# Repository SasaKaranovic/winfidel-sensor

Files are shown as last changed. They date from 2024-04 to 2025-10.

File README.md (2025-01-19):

# WInFiDEL Sensor

**W**ireless
**In**line
**Fi**lament
**D**iameter
**E**stimator
**L**ow-cost
Sensor

## What is WInFiDEL?

WInFiDEL (https://www.youtube.com/watch?v=FzXX6JxIw_Q "WInFiDEL - DIY 3D Printing Filament Diameter Sensor")

[WInFiDEL Video](https://www.youtube.com/watch?v=FzXX6JxIw_Q)

WInFiDEL is an DIY open-source open-hardware Wireless 3D printing filament diameter sensor.

This design is heavily inspired by the design previously published by Made with Layers (Thomas Sanladerer) (video: https://www.youtube.com/watch?v=RYgdLPe_T0c)

## Can I build my own WInFiDEL sensor?

Yes! All the source files (hardware and firmware) are available in this repository.

## Can I purchase WInFiDEL PCBA?

Yes! It's available on the [web shop](https://shop.sasakaranovic.com/products/winfidel).

## Where can I find documentation?

WInFiDEL documentation can be found on the [official documentation page](https://docs.sasakaranovic.com/winfidel/).

## Screenshots

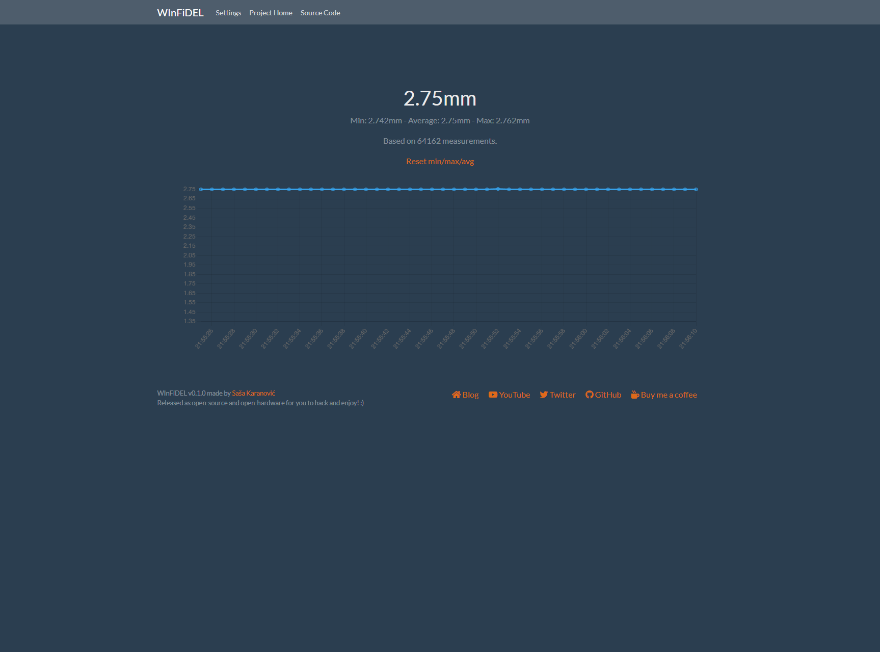
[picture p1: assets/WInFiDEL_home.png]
Home


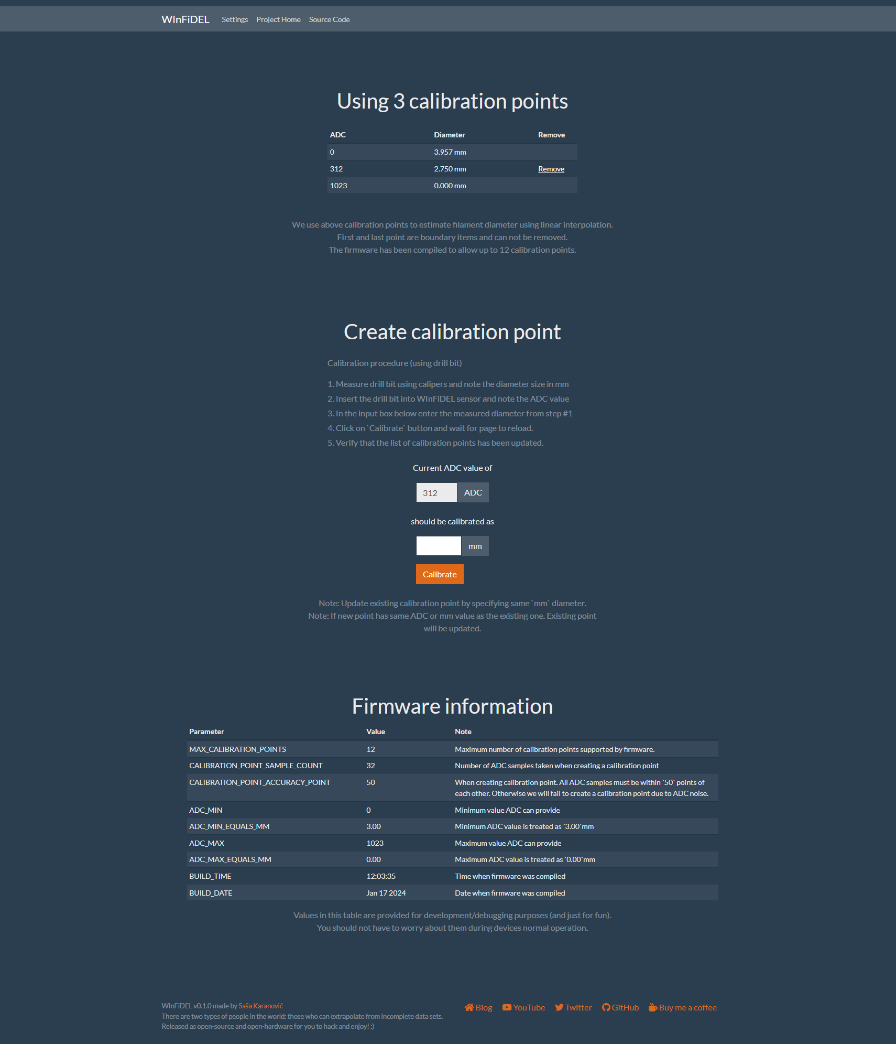
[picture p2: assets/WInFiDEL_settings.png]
Calibration


## Sasa Karanovic

<a href="https://sasakaranovic.com/" target="_blank" title="Sasa Karanovic Home Page"> Home Page</a> &nbsp;&middot;&nbsp;
<a href="https://youtube.com/c/sasakaranovic" target="_blank" title="Sasa Karanovic on YouTube"> YouTube</a> &nbsp;&middot;&nbsp;
<a href="https://github.com/sasakaranovic" target="_blank" title="Sasa Karanovic on GitHub"> GitHub</a> &nbsp;&middot;&nbsp;
<a href="https://twitter.com/_sasakaranovic_" target="_blank" title="Sasa Karanovic on Twitter"> Twitter</a> &nbsp;&middot;&nbsp;
<a href="https://instagram.com/_sasakaranovic_" target="_blank" title="Sasa Karanovic on Instagram"> Instagram</a> &nbsp;&middot;&nbsp;
<a href="https://github.com/sponsors/SasaKaranovic" target="_blank" title="Sponsor on GitHub"> Sponsor on GitHub</a>

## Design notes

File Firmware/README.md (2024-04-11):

# How to build firmware

For our firmware development, we are going to use Arduino. Mainly because it's user friendly, easy to use and
most hobbyists are familiar with it or have already used it. While we could build the same or even more efficient
firmware using bare-metal C and ESP-IDF, we are going to stick with Arduino and hope that this allows the project to be
more friendly and easier to use/modify by wider DIY/hacker community.

## How can I build/compile firmware?

### 1. Install PlatformIO
Installing PlatformIO CLI is pretty straight-forward and also well documented for Windows, Linux and MacOS.
You will need to follow few steps and get PlatformIO CLI installed, detailed tutorial can be found at https://platformio.org/install/cli
Make sure to install [PlatformIO Core](https://docs.platformio.org/en/latest//core/installation.html#installation-methods 'https://docs.platformio.org/en/latest//core/installation.html#installation-methods') and allso that it is available trough [shell](https://docs.platformio.org/en/latest//core/installation.html#piocore-install-shell-commands 'PlatformIO Core - Install Shell Commands¶').

### 2. Build firmware
Open shell/command-prompt and navigate to 'Firmware/platformio' folder.

1. Compile and upload the firmware with `pio run --target upload --upload-port <COM-PORT>`. Make sure to replace `<COM-PORT>` with your ESP32's COM port (ie COM1 or /dev/ttyACM0)
2. Upload the file system (Web page) with `pio run --target uploadfs --upload-port <COM-PORT>`, again replace `<COM-PORT>` with your ESP32's COM port.
3. Restart/power-cycle your board

Every time you make a firmware change, you need to run step #1.
Every time you make a change to the web page (anything inside `data` folder) you only need to run step #2.

[<- Go back to repository root](../README.md)

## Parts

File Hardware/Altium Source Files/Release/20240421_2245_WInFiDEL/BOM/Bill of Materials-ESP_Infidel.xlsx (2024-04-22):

Designator | Value | Description | Distributor | Distributor Part Number | Manufacturer | Manufacturer Part Number | Quantity | Footprint
A1 |  | RF ANT 2.45GHZ CHIP SOLDER SMD | LCSC | ANT3216LL00R2400A | YAGEO | ANT3216LL00R2400A | 1 | ANT3216LL00R2400A
C1, C6 | 22uF | Capacitor | LCSC | C602037 | Samsung Electro-Mechanics | CL21A226MAYNNNE | 2 | 0805
C2, C5, C15, C24, C25 | 10uF | Capacitor | LCSC | C15850 | Samsung Electro-Mechanics | CL21A106KAYNNNE | 5 | 0603 - CAP
C3, C4, C11, C13, C16, C20, C21, C22, C23 | 100n | Capacitor | LCSC | C1591 | Samsung Electro-Mechanics | CL10B104KB8NNNC | 9 | 0603 - CAP
C9, C10, C12, C14, C17 | 1u | Capacitor | LCSC | C559769 | YAGEO | CC0603KRX7R9BB105 | 5 | 0603 - CAP
C18, C19 | 8pF | Capacitor | LCSC | C327316 | YAGEO | CC0603CRNPO9BN8R0 | 2 | 0603 - CAP
P1 |  | 3A 1 Surface Mount 16P Female -25℃~+85℃ Type-C SMD USB Connectors ROHS | LCSC | C2927039 | DEALON | USB-TYPE-C-019 | 1 | GCT_USB4105-GF-A
R1, R2, R5, R6, R7, R8 | 5.1K | Resistor | LCSC | C105580 | YAGEO | RC0603FR-075K1L | 6 | 0603
R3, R4 | 27R | Resistor | LCSC | C137753 | YAGEO | RC0603FR-0727RL | 2 | 0603
R9, R10, R12 | 2K2 | Resistor | LCSC | C125931 | YAGEO | AC0603FR-072K2L | 3 | 0603
R11 | 0R | Resistor | LCSC | C95177 | YAGEO | RC0603JR-070RL | 1 | 0603
SW1, SW2 |  | 50mA Surface Mount SPST 100MΩ 100,000 Times 12V 160gf@±50gf SMD Tactile Switches ROHS | LCSC | C7498203 | Lian Xin Technology | XDTD-0304-215 | 2 | Switch-XDTD-0304-215
U1 |  | 600mA null 3.3V positive 6V SOT-25 Linear Voltage Regulators (LDO) ROHS | LCSC | C526385 | Diodes Incorporated | AP7366-33W5-7 | 1 | SOT-23-5
U2 |  | Ultra-Low-Power SoC with RISC-V Single-Core CPU 2.4 GHz Wi-Fi (802.11 b/g/n) and Bluetooth® 5 (LE) | LCSC | C2858491 | Espressif Systems | ESP32-C3FH4 | 1 | QFN50P500X500X100_HS-33N
U3 |  | Hall Effect Sensor Single Axis Radial Lead | LCSC | C266124 | Texas Instruments | DRV5055A3QLPGM | 1 | SS490A
U4 |  | 10 Bit Analog to Digital Converter 1 Input 1 SAR SOT-23-5 | LCSC | C625475 | Microchip Technology | MCP3221A5T-E/OT | 1 | SOT95P270X145-5N
X1 |  | 40MHz 9pF ±10ppm SMD2016-4P Crystals ROHS | LCSC | C2929402 | TROQ | R940000171 | 1 | XTAL-4LEAD-2016

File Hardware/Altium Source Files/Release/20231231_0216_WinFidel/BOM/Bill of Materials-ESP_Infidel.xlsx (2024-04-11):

Designator | Description | Distributor | Distributor Part Number | Manufacturer | Manufacturer Part Number | Quantity
A1 | RF ANT 2.45GHZ CHIP SOLDER SMD | LCSC | ANT3216LL00R2400A | YAGEO | ANT3216LL00R2400A | 1
C1, C6 | Capacitor | DigiKey | 1276-CL21A226MAYNNNECT-ND | Samsung Electro-Mechanics | CL21A226MAYNNNE | 2
C2, C5 | Capacitor | DigiKey | 1276-2891-1-ND | Samsung Electro-Mechanics | CL21A106KAYNNNE | 2
C3, C4 | Capacitor | DigiKey | 1276-1009-1-ND | Samsung Electro-Mechanics | CL10B103KB8NNNC | 2
C7, C8, C9, C10, C11, C12, C13, C14, C15, C16, C17, C18, C19, C20, C21, C22, P2, R1, R2, R3, R4, R6, R7, R8, R9, R10, R11, R12, U2 | Capacitor, Header, 5-Pin, Resistor, Ultra-Low-Power SoC with RISC-V Single-Core CPU 2.4 GHz Wi-Fi (802.11 b/g/n) and Bluetooth® 5 (LE) | [NoValue], DigiKey, LCSC | [NoValue], C2858491 | [NoValue], Espressif Systems |  | 29
P1 | 3A 1 Surface Mount 16P Female -25℃~+85℃ Type-C SMD USB Connectors ROHS | LCSC | C2927039 | DEALON | USB-TYPE-C-019 | 1
SW1, SW2 | 50mA Surface Mount SPST 100MΩ 100,000 Times 12V 160gf@±50gf SMD Tactile Switches ROHS | LCSC | C7498203 | Lian Xin Technology | XDTD-0304-215 | 2
U1 | 600mA null 3.3V positive 6V SOT-25 Linear Voltage Regulators (LDO) ROHS | LCSC | C526385 | Diodes Incorporated | AP7366-33W5-7 | 1
U3 | Hall Effect Sensor Single Axis Radial Lead | DigiKey | 296-DRV5055A2QLPGMCT-ND | Texas Instruments | DRV5055A2QLPGM | 1
U4 | 10 Bit Analog to Digital Converter 1 Input 1 SAR SOT-23-5 | DigiKey | MCP3021A5T-E/OTCT-ND | Microchip Technology | MCP3021A5T-E/OT | 1
X1 | 40MHz 9pF ±10ppm SMD2016-4P Crystals ROHS | LCSC | C2929402 | TROQ | R940000171 | 1

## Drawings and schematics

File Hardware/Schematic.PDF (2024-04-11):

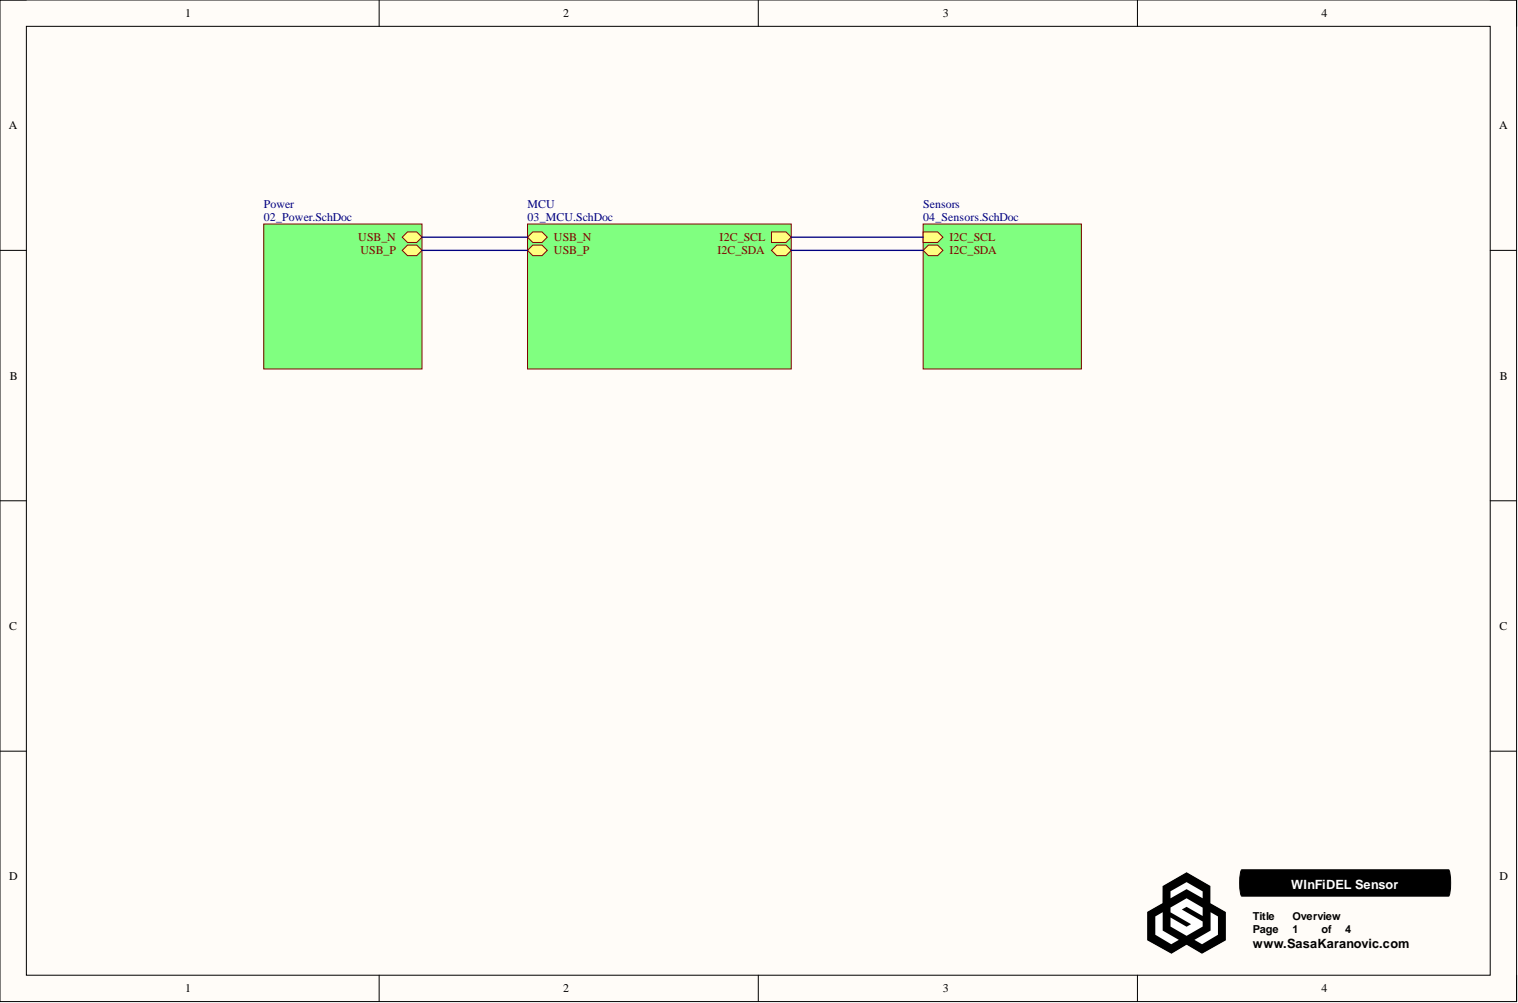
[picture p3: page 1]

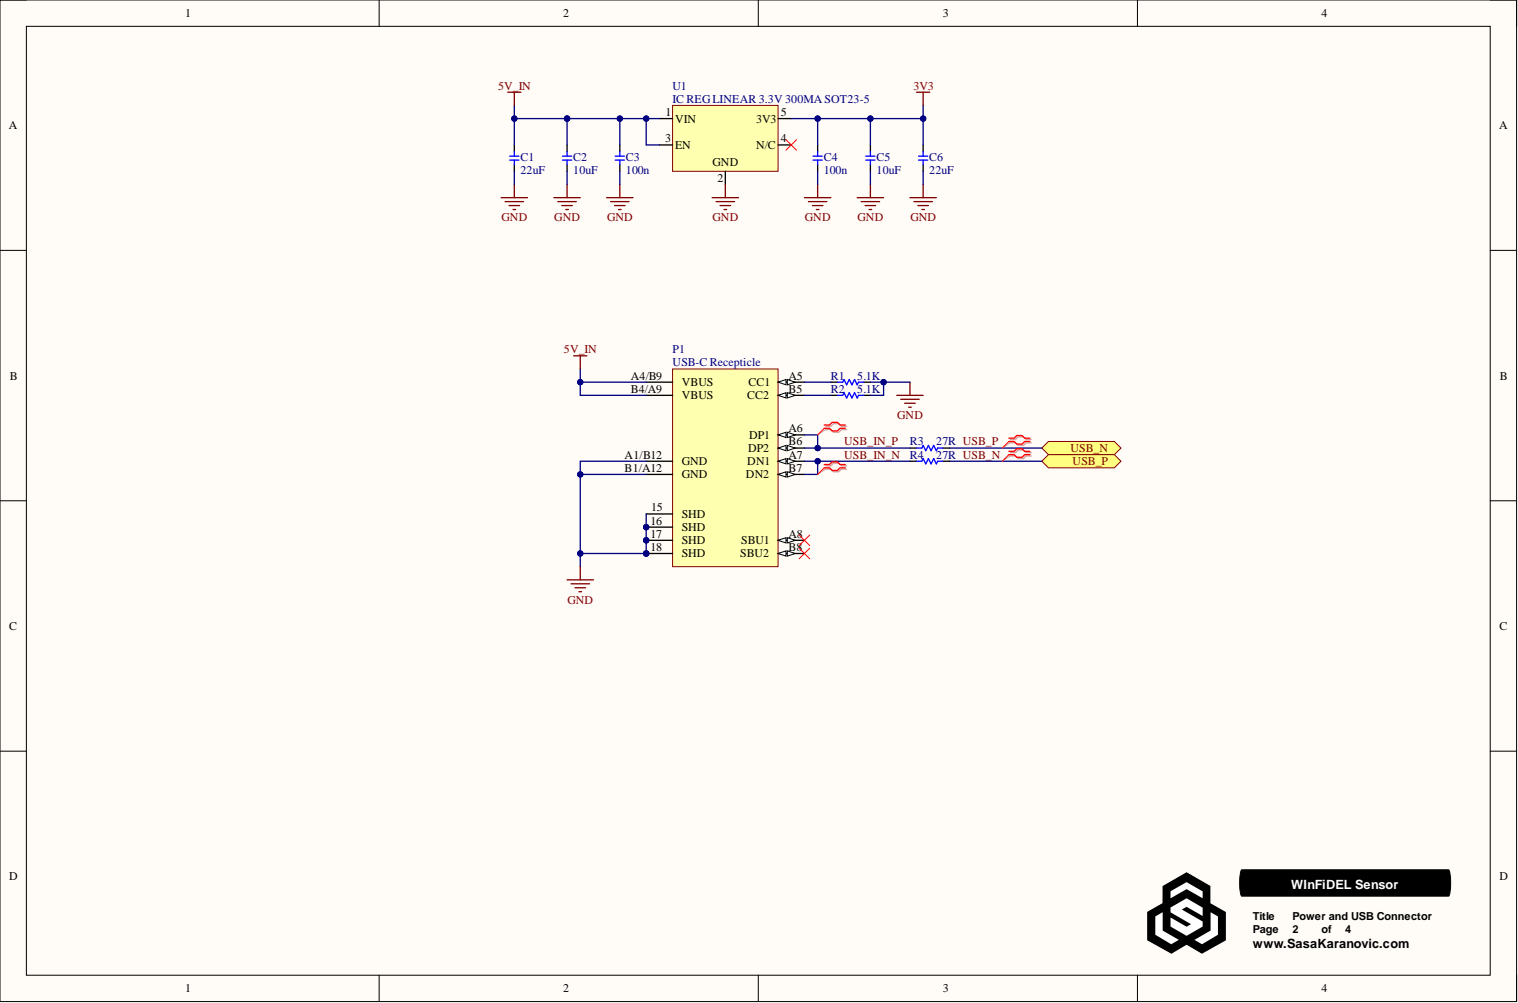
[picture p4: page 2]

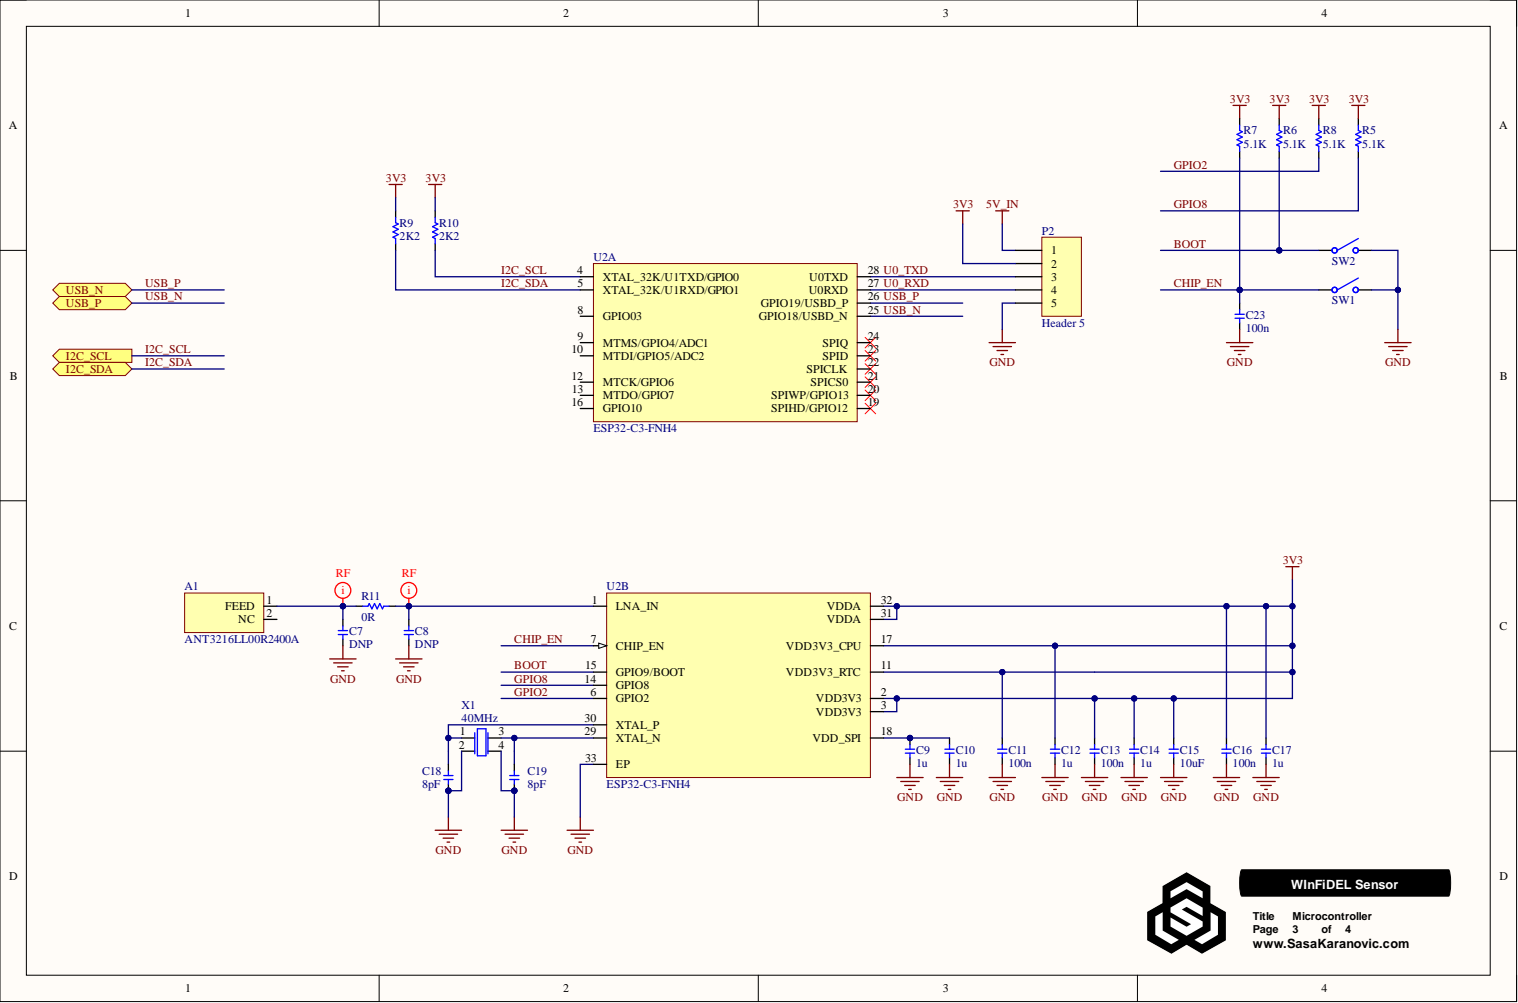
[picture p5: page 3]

GPIO2

GPIO8

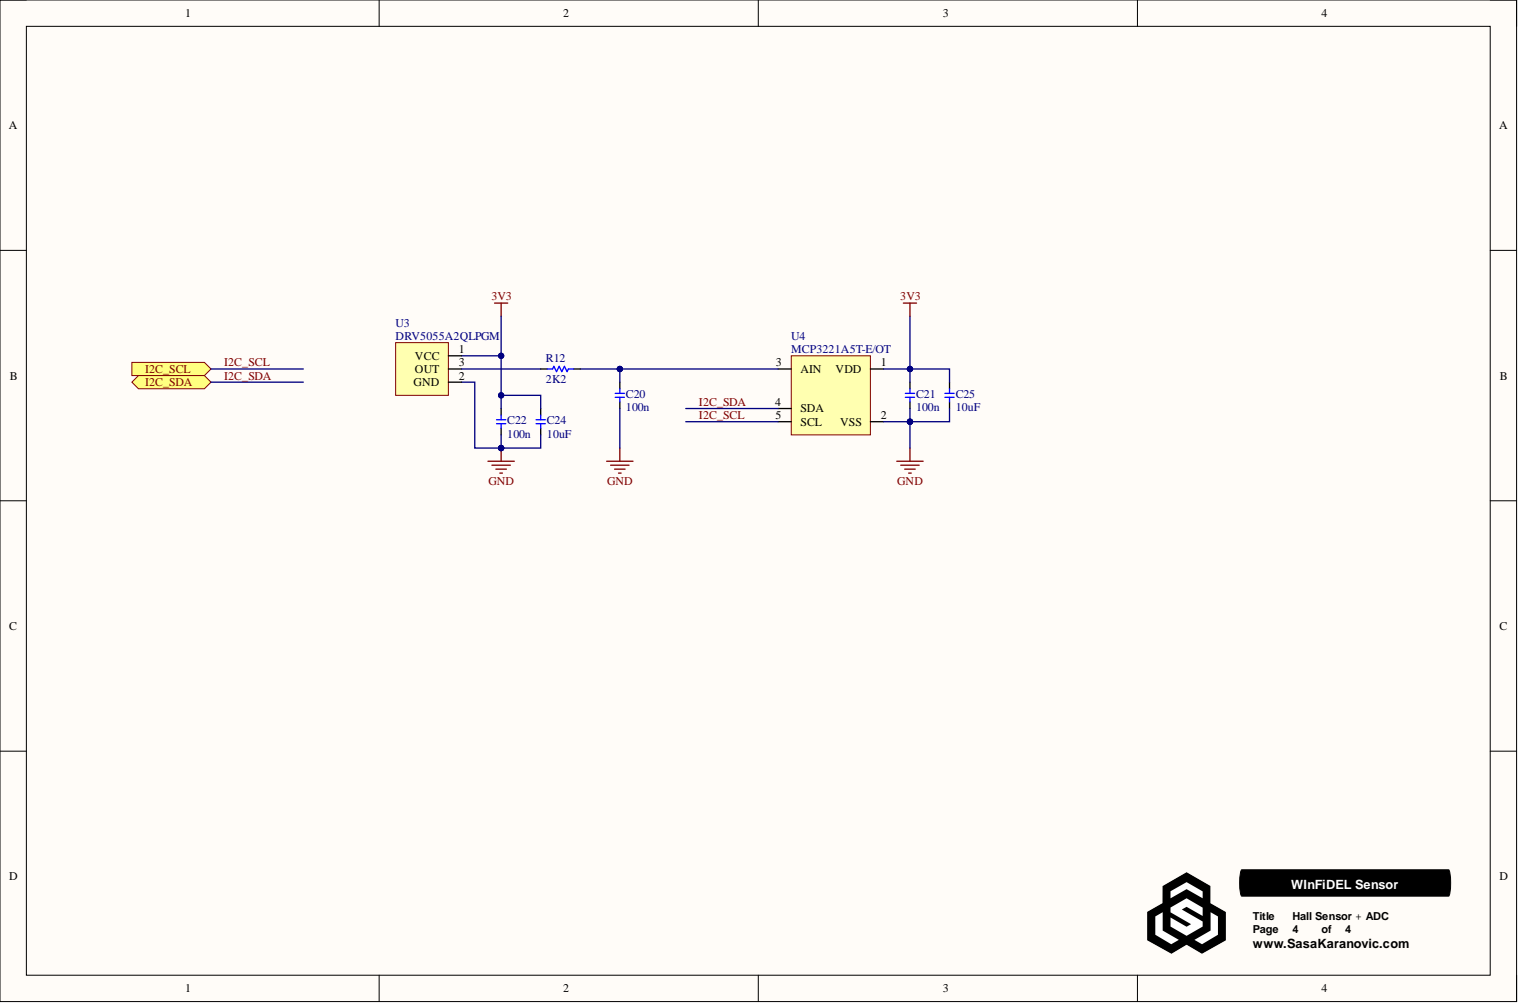
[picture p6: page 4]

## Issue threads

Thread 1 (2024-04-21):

Provided Gerber does not match Altium Data

cad435, 2024-04-21:
through sheer coincidence I just found out:

Just an example:

Gerber Data
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

Altium Data:
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

SasaKaranovic, 2024-04-22:
Thanks for mentioning this! I have just exported another gerber release that contains latest design. So everything should be good to go now.

If you look at the Gerbers, the silkscreen says "2023-DEC" but the Altium files have "2024-FEB".
This release was "rushed" in order to make sure people have all the source files available before Stefan's video goes live.

Closed 2024-04-22.

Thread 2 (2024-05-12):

LittleFS mount fail on new device

cad435, 2024-05-12:
Hello!

After building the devices (PnP as per BOM, used JLCPCBA) i get the following error:

```Starting...
*wm:AutoConnect
*wm:Connecting to SAVED AP: ***
*wm:connectTimeout not set, ESP waitForConnectResult...
*wm:AutoConnect: SUCCESS
*wm:STA IP Address: 192.168.178.72
Connected.
Starting LittleFS...E (11254) esp_littlefs: ./components/esp_littlefs/src/littlefs/lfs.c:1367:error: Corrupted dir pair at {0x0, 0x1}

E (11255) esp_littlefs: mount failed,  (-84)
E (11258) esp_littlefs: Failed to initialize LittleFS
[ 11148][E][LittleFS.cpp:98] begin(): Mounting LittleFS failed! Error: -1
An Error has occurred while mounting LittleFS
```

Any thoughts what went wrong?

cad435, 2024-05-12:
Just realized I forgot to build and upload the filesystem contents...

PEBCAK error I suppose :)

SasaKaranovic, 2024-05-12:
Been there done that. :)
Glad you figured it out. Let me know how it works.

Would you mind sharing how much did the PCBA run cost?
I know there are others that are interested in ordering these. I received couple of emails asking how much would it cost to make 1/5/10 of these through one of the online PCB services.

cad435, 2024-05-12:
Sure!

5 pcs cost me 36.84€ shipped.

Mind you, the USB-C connector, ADC, LDO, the tactile swithces and the 8pf capacitors I soldered myself. I have those laying around and did not want to spend the additional cost on those.
The problem is, those are "non standard" components for JLC so they take 3$ setup fee per component, which would increase the cost by 15$.
I was willing to take that for the ESP as I had not laying those around.

if you go all in I'd suppose you'll end up on about 50-60€ shipped for 5 pcs and about 90-100€ for 10pcs.

SasaKaranovic, 2024-05-12:
Awesome! Thank you for sharing this. I'm sure others will be happy to have a rough estimate on how much everything cost.

Closed 2024-05-12.

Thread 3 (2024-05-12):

Hall Sensor Reversed

cad435, 2024-05-12:
It should be noted somewhere, that the hall sensor should be mounted the other way round, compared to the original INFIDEL Sensor.

Top-PCB is the original, bottom PCB is WinFIDEL

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

Therefore the Hall-effect sensor must be glued in "upside down" compared to the original.

 - cad435

SasaKaranovic, 2024-05-13:
Hey @cad435

Please note that while WInFiDEL is inspired by InFiDEL, it is not identical, obviously.
If you flip the WInFiDEL board, you should see the 3V3, GND and OUT markings for that IC.

There are two ways you can figure out which components is on which side.
- Manually: If you use silkscreen as your guide, there is silkscreen on top AND bottom side. On the bottom side there is silkscreen that indicates the sensor pinout and also U3 that indicates that hall effect sensor is on the bottom.
- Production: Pick and Place file indicates that the U3 is on the bottom side.

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

SasaKaranovic, 2024-05-13:
I don't have the InFiDEL sensor but just looked at some pictures and it looks like the sensor is mounted in the exact same way on the exact same side.

Can you clarify what do you mean by `the hall sensor should be mounted the other way round` ?
Are you using the Hall effect sensor that is specified by WInFiDEL design (ie `DRV5055A3`/`DRV5055A2`/`DRV5055A1`) ?

cad435, 2024-05-13:
Yes, I use a DRV5505.

So basically I hat some IFIDELS laying around and "upgraded" them with WinFIDEL.

The problem is as followed:
While INFIDEL hast the VIN pin of the hall-Sensor on the right pin (in my top picture), WinFIDEL has the VIN pin on the Left side.

So in order to upgrade from INFIDEL to WinFIDEL I had to remove the HALL sensor and glue a new one in, to match the Pinout.

And it works now 👌🏼

SasaKaranovic, 2024-05-14:
Glad to hear that you got it working.

I'm not sure where did this suggestion that WInFiDEL and InFiDEL are pin-to-pin compatible came from?
These are two different designs that share some design features but that's pretty much it.

Closed 2024-05-14.

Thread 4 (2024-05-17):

What hall effect sensor and magnet combination should I use?

SasaKaranovic, 2024-05-17:
WInFiDEL being an open-source open-hardware DIY project means that at some point this question will come up.

The sensor that is mentioned in the video/BOM/design is `DRV5055Ax` where `x` can be a number `1-4`.
This means that this sensor comes in four variants that are (in order from most-sensitive to least-sensitive) `A1`, `A2`, `A3`, `A4`.

```
From the datasheet:
– A1: 100 mV/mT, ±21-mT Range
– A2: 50 mV/mT, ±42-mT Range
– A3: 25 mV/mT, ±85-mT Range
– A4: 12.5 mV/mT, ±169-mT Range
```

### Which sensor out of these four will work?
Short answer: All of them.
Long answer: All of them, but some might give you more accuracy/range.

### How to select "the one"
To find the perfect one, it might require some trial and error or "guesstimation".
If you have a bigger magnet, you might want to select a less-sensitive sensor in order to have more range, and vice-versa.

Ideally when the sensor is "empty" (nothing inside), you should get ADC reading that is close to full scale (2048)
Then if you manually "open the sensor" (lift the sensor arm as far as it goes), you should get the ADC reading that is very low (ideally anything below ~300-400 should be good).

Keep in mind that you have two variables to play with; you can either change the sensor, or change the magnet.
There is also the third option of modifying the 3D printed parts if you are up to it.

SasaKaranovic, 2024-05-17:
So far I have built at least five WInFiDEL sensors .

The combination of magnet + sensor that worked well was:
- A tiny magnet. Unfortunately I bought it on AliExpress a while back so no datasheet for it. It's roughly R=5mm and H=1mm
- `A2`/`A3` sensor variant

Please feel free to help others and contribute by adding which sensor and magnet combination you have used and what are the ADC min/max readings that you get.

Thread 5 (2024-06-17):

C7, C8 are DNP and not in the BOM. What does DNP mean?

johndeere6110, 2024-06-17:
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

hello

When I want to buy the PCB, I am asked what should be placed in these places and I cannot find what should be placed there, can you help me?

SasaKaranovic, 2024-06-18:
Please take a look at the schematic and/or BOM.
Components that you marked are A1, C7, R11, C8 from left to right respectively.

johndeere6110, 2024-06-18:
I understand, but I can find it in the schematic, but it is not in the BOM so I don't know which capacitor should be there.
[Bill of Materials-ESP_Infidel.xlsx](https://github.com/user-attachments/files/15890868/Bill.of.Materials-ESP_Infidel.xlsx)
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

SasaKaranovic, 2024-06-20:
@johndeere6110 those parts are marked as DNP or Do Not Populate. Also sometimes interpreted as do not purchase/place etc) and they will not appear in the BOM.
So you would not solder these components on the board.

You might ask "Why then put them in the design if you know you are not going to populate them?"
There are many valid reasons to do so. In this particular case these are placeholders to be used used for antenna tuning.

Closed 2025-01-11.

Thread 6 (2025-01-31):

Location of STL files

CBoismenu, 2025-01-31:
Just purchased one of the PCB but I can't find the stl files to print the enclosure.

Are we suppose  to use the stl from the infidel files.

Thanks for your help

SasaKaranovic, 2025-02-01:
Hey @CBoismenu

In the video I have used the STL files from the InFiDEL repository.
So all parts (3D printed and mechanical) should work.

Let me know if this helps.
Also if someone ends up designing/remixing the enclosure, please feel free to share.

Closed 2025-02-15.

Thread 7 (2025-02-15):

Integration in Klipper

CBoismenu, 2025-02-15:
Recently bought one of your PCB's and constructed the "Winfidel".

It works perfectly.

Would like to integrate it with klipper via USB but can't seem to find information on how to do that.

Would you happen to have any kind of information on the subject.

Thanks in advance for your help.

SasaKaranovic, 2025-02-22:
Hey @CBoismenu

I have just added a documentation for the [web API](https://docs.sasakaranovic.com/winfidel/web_api/).

Couple of people have also asked about using the WInFiDEL through USB/Serial instead of web API so I have updated the firmware to also print out the diameter over USB/serial ([docs](https://docs.sasakaranovic.com/winfidel/usb_api/)].

Let me know if you need any help or support from my side.
Also if you could share you Klipper integration with others, that would be greatly appreciated.

CBoismenu, 2025-02-22:
Documentation is interesting.

I will have to investigate furthermore if and how I would implement that in klipper.

I must admit though that my knowledge on how to do that is somewhat lacking.

I I find anything usefull I will relay the information.

Again thanks for your help.

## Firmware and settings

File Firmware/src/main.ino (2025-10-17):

#include <ESPmDNS.h>
#include <EEPROM.h>
#include <WiFiManager.h>
#include <ArduinoOTA.h>
#include "WiFi.h"
#include "ESPAsyncWebServer.h"
#include "include/PersistSettings.h"
#include "config_winfidel.h"

bool bStatusLED = false;

#if CONFIG_ENABLE_WIFI
WiFiManager wifiManager;
AsyncWebServer server(80);
volatile int WiFi_status = WL_IDLE_STATUS;
const char mdnsName[] = MDNS_NAME;
const char wifiName[] = WIFI_HOSTNAME;
uint8_t dbgOTApercent = 100;
#endif //CONFIG_ENABLE_WIFI

#if CONFIG_PRINT_MEASUREMENTS_USB_CDC
int SerialInByte = 0;
bool bSerialPrintoutRequested = false;
#endif // CONFIG_PRINT_MEASUREMENTS_USB_CDC

void setup()
{
    pinMode(LED_RED_PIN, OUTPUT);
    digitalWrite(LED_RED_PIN, HIGH);
    pinMode(LED_GREEN_PIN, OUTPUT);
    digitalWrite(LED_GREEN_PIN, HIGH);
    pinMode(LED_BLUE_PIN, OUTPUT);
    digitalWrite(LED_BLUE_PIN, HIGH);

    LED_RED_ON();

    // Configure Serial communication
	Serial.begin(115200);   // USB-to-UART
    Serial0.begin(115200);  // TX/RX GPIOS

    Serial.println("Wireless Inline Filament Estimator, Low-Cost - WInFiDEL");
    Serial0.println("Wireless Inline Filament Estimator, Low-Cost - WInFiDEL");

#if CONFIG_ENABLE_WIFI
    WiFi.setHostname(wifiName);
#endif // CONFIG_ENABLE_WIFI

    delay(500);

    LED_GREEN_ON();

#if CONFIG_ENABLE_WIFI
    bool res;
    res = wifiManager.autoConnect("SK-WInFiDEL-Setup");

    if(!res) {
        Serial.println("Failed to connect or hit timeout");
        ESP.restart();
    }
    else {
        //if you get here you have connected to the WiFi
        Serial.println("Connected.");
    }

	Serial.print("WiFi IP: ");
	Serial.println(WiFi.localIP());

    if (!MDNS.begin(mdnsName))
    {
        Serial.println("Error starting mDNS");
    }
    else
    {
        Serial.println((String) "mDNS http://" + MDNS_NAME + ".local");
    }

    // Add service to MDNS-SD
    MDNS.addService("http", "tcp", 80);
#endif // CONFIG_ENABLE_WIFI

    EEPROM.begin(sizeof(calibration_t));
    calibration_init();

    adc_init();

#if CONFIG_ENABLE_WIFI
    Serial.print("Starting WebServer...");
	setupWebServer();
	server.begin();
    Serial.println("done.");

    Serial.print("WiFi IP: ");
    Serial.println(WiFi.localIP());

    /**
    * Enable OTA update
    */
    ArduinoOTA
    .onStart([]() {
      String type;
      if (ArduinoOTA.getCommand() == U_FLASH)
        type = "sketch";
      else // U_SPIFFS
        type = "filesystem";

      // NOTE: if updating SPIFFS this would be the place to unmount SPIFFS using SPIFFS.end()
      Serial.println("Start updating " + type);
    })
    .onEnd([]() {
      Serial.println("\nEnd");
    })
    .onProgress([](unsigned int progress, unsigned int total) {
        uint8_t percent = (progress / (total / 100));
        if (percent == dbgOTApercent)
        {
            return;
        }
        if ((percent%5) == 0)
        {
            Serial.printf("Progress: %u%%\r", percent);
            dbgOTApercent = percent;
        }
    })
    .onError([](ota_error_t error) {
      Serial.printf("Error[%u]: ", error);
      if (error == OTA_AUTH_ERROR) Serial.println("Auth Failed");
      else if (error == OTA_BEGIN_ERROR) Serial.println("Begin Failed");
      else if (error == OTA_CONNECT_ERROR) Serial.println("Connect Failed");
      else if (error == OTA_RECEIVE_ERROR) Serial.println("Receive Failed");
      else if (error == OTA_END_ERROR) Serial.println("End Failed");
    });
    ArduinoOTA.begin();
    Serial.println("Arduino OTA is on");
#endif // CONFIG_ENABLE_WIFI

    // Debug message to signal we are initialized and entering loop
	Serial.println("Ready to go.");

    i2c_scan_bus();
    LED_RED_OFF();

    Serial.println("Entering main loop");
    LED_RED_OFF();
    LED_GREEN_OFF();
    LED_BLUE_OFF();
}


void loop()
{
    Measurements_Tick();

#if CONFIG_ENABLE_WIFI
    ArduinoOTA.handle();
#endif // CONFIG_ENABLE_WIFI

#ifdef CONFIG_PRINT_MEASUREMENTS_USB_CDC
    int available = Serial.available();
    if(available > 0)
    {
        SerialInByte = Serial.read();
        if(SerialInByte == 'S' || SerialInByte == 's')
        {
            bSerialPrintoutRequested = true;
        }
        else if(SerialInByte == 'E' || SerialInByte == 'e')
        {
            bSerialPrintoutRequested = false;
            LED_SERIAL_OFF();
        }
    }
#endif // CONFIG_PRINT_MEASUREMENTS_USB_CDC
}

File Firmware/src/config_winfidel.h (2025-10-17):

#ifndef __WINFIDEL_CFG__
#define __WINFIDEL_CFG__

#define MDNS_NAME       "winfidel"
#define WIFI_HOSTNAME   "WInFiDEL by SK"

#ifndef CONFIG_PRINT_MEASUREMENTS_USB_CDC
#define CONFIG_PRINT_MEASUREMENTS_USB_CDC   1       // Set to `1` if we want serial (USB-to-Serial) printout for every measurement.
#endif // CONFIG_PRINT_MEASUREMENTS_USB_CDC

#ifndef CONFIG_PRINT_MEASUREMENTS_UART_GPIO
#define CONFIG_PRINT_MEASUREMENTS_UART_GPIO 1       // Set to `1` if we want serial (TX GPIO) printout for every measurement.
#endif // CONFIG_PRINT_MEASUREMENTS_UART_GPIO

#ifndef CONFIG_ENABLE_WIFI
#define CONFIG_ENABLE_WIFI                  1       // Set to `1` if we want to use WiFi (ie not requred for Serial only application)
#endif

#define CALIBRATION_POINT_SAMPLE_COUNT      32      // Number of ADC samples to take for new calibration point
#define CALIBRATION_POINT_ACCURACY_POINT    50      // We expect all CALIBRATION_POINT_SAMPLE_COUNT samples to be
                                                    // within CALIBRATION_POINT_ACCURACY_POINT of each other
                                                    // in order to have successful calibration point creation

#define CALIBRATION_BOUNDARY_ITEMS          2       // We need lower and upper boundary item for safety
#define MAX_CALIBRATION_POINTS              (10 + CALIBRATION_BOUNDARY_ITEMS)
#define ADC_MIN                             0       // Minimum value we can get from our ADC (should be always 0)
#define ADC_MIN_EQUALS_MM                   5.0f    // ADC_MIN should be considered this diameter (in mm)
#define ADC_MAX                             4095    // Maximum value we can get from our ADC (should be 2^n-bits)
#define ADC_MAX_EQUALS_MM                   0.0f    // ADC_MAX should be considered this diameter (in mm)

#define CAL_POINT_EMPTY                     { .adc = ADC_MIN, .mm = ADC_MIN_EQUALS_MM }
#define CAL_POINT_FIRST                     { .adc = ADC_MIN, .mm = ADC_MIN_EQUALS_MM }
#define CAL_POINT_LAST                      { .adc = ADC_MAX, .mm = ADC_MAX_EQUALS_MM }


#define ADC_MAX_SAMPLES                     64      // Maximum number of ADC samples we can take in one measurement cycle
#define ADC_SAMPLES_PER_MEASUREMENT_CYCLE   16      // How many samples to take for each measurement cycle
#define ADC_FINAL_ADC_VALUE_USING_MEAN              // Use mean instead of average ADC value

#define ADC_CHIP_IS_MCP3221                         // Specify which ADC chip we are using
// #define ADC_CHIP_MCP3021                            // Specify which ADC chip we are using
#define ADC_I2C_ADDRESS                     0x4D    // 7-bit I2C address of our ADC IC
#define I2C_SCL_PIN                         0       // SCL pin number
#define I2C_SDA_PIN                         1       // SDA pin number

#define LED_RED_PIN                         5       // RED LED pin number
#define LED_GREEN_PIN                       4       // GREEN LED pin number
#define LED_BLUE_PIN                        3       // BLUE LED pin number
#define LED_MEASUREMENT_PIN                 LED_GREEN_PIN
#define LED_SERIAL_PIN                      LED_BLUE_PIN

#define LED_RED_ON()                        do { digitalWrite(LED_RED_PIN, LOW); } while(0)
#define LED_RED_OFF()                       do { digitalWrite(LED_RED_PIN, HIGH); } while(0)
#define LED_GREEN_ON()                      do { digitalWrite(LED_GREEN_PIN, LOW); } while(0)
#define LED_GREEN_OFF()                     do { digitalWrite(LED_GREEN_PIN, HIGH); } while(0)
#define LED_BLUE_ON()                       do { digitalWrite(LED_BLUE_PIN, LOW); } while(0)
#define LED_BLUE_OFF()                      do { digitalWrite(LED_BLUE_PIN, HIGH); } while(0)
#define LED_MEASUREMENT_ON()                do { digitalWrite(LED_MEASUREMENT_PIN, LOW); } while(0)
#define LED_MEASUREMENT_OFF()               do { digitalWrite(LED_MEASUREMENT_PIN, HIGH); } while(0)
#define LED_SERIAL_ON()                     do { digitalWrite(LED_SERIAL_PIN, LOW); } while(0)
#define LED_SERIAL_OFF()                    do { digitalWrite(LED_SERIAL_PIN, HIGH); } while(0)

// String buffers
#define SENSOR_STR_MAX_LEN                  256
#define CALIBRATION_JSON_STR_MAX_LEN        512

#define EEPROM_MAGIC_KEY                    0x53    // Predefined value used to verify EEPROM has been initialized


// Enum holding calibration results
typedef enum winfidel_status
{
    WINFIDEL_OK,
    WINFIDEL_FAIL,
    WINFIDEL_FORBIDDEN,
    WINFIDEL_INVALID_ARGUMENT,
    WINFIDEL_MISSING,
    WINFIDEL_NO_SPACE,
    WINFIDEL_LOW_ACCURACY

} winfidel_status_t;


// Calibration point struct -> holds ADC value and equivalent mm diameter
typedef struct cal_point
{
    uint32_t adc;
    float mm;
} cal_point_t;

// Calibration struct -> holds all calibration points and total number of valid calibration points
typedef struct calibration
{
    cal_point_t points[MAX_CALIBRATION_POINTS];
    uint32_t numPoints;
    uint8_t valid;
} calibration_t;
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

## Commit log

2024-04-22 Adding latest release files.
    [Bill of Materials-ESP_Infidel.xlsx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]
2025-02-22 Updating WInFiDEL API path to include API version. Adding diameter serial printout.
2025-02-22 Adding Start/End serial printout commands. Updating RGB LED meaning to `green->web`, `teal->web+serial`.
2025-10-17 Adding explicit config option to enable/disable WiFi, USB-to-Serial and Serial printing. Printing measurements to Serial is now always on by default.
